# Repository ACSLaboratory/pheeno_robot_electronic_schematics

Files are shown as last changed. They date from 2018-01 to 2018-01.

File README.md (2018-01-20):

# pheeno_robot_electronic_schematics

## Pheeno Version 2.0

This is the ACSLab GitHub repository for the files relating to the electronic construction of the Pheeno robot platform. Pheeno is designed to be an inexpensive (cost of parts = $420), research-level platform for multi-robot experiments, robotics education, and outreach activities. This repository will be updated with additional modules, code, and improvements to existing modules as they are developed.

Thanks for checking out the robot!

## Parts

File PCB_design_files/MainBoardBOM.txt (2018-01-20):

"Id";"Designator";"Package";"Quantity";"Designation";"Supplier and ref";
1;"P9";"Pin_Header_Straight_1x04";1;"GPIO JUMPER";;;
2;"IRLF1,IRR1,IRB1,IRF1,IRL1,IRRF1";"GP2Y0A41SK0F";6;"GP2Y0A41SK0F";;;
3;"C17,C16,C15,C14,C13,C12,C11,C10,C9,C8,C7,C3";"C_Rect_L7_W2_P5";12;"0.1uF";;;
4;"C2,C1";"C_Rect_L7_W2_P5";2;"1uF";;;
5;"C4";"C_Radial_D10_L25_P5";1;"1000uF";;;
6;"P2";"Pin_Header_Straight_1x02";1;"Raspberry Pi Power";;;
7;"R1";"Resistor_Horizontal_RM7mm";1;"61.9k";;;
8;"R2,R3,R5";"Resistor_Horizontal_RM7mm";3;"49.9k";;;
9;"R4,R6";"Resistor_Horizontal_RM7mm";2;"1M";;;
10;"R8";"Resistor_Horizontal_RM7mm";1;"30k";;;
11;"R9,R14,R15,R16,R17,R18,R19";"Resistor_Horizontal_RM7mm";7;"10k";;;
12;"R10";"Resistor_Horizontal_RM7mm";1;"499";;;
13;"P1";"Molex_KK-6410-02_02x2.54mm_Straight";1;"12V Power";;;
14;"BT1";"Pin_Header_Straight_1x02";1;"11.1V";;;
15;"C5";"C_Radial_D10_L16_P5";1;"470uF";;;
16;"C6,C18,C19,C20,C21,C22,C23";"C_Radial_D4_P1.5";7;"10uF";;;
17;"D1";"Molex_KK-6410-02_02x2.54mm_Straight";1;"LED";;;
18;"IMU1";"Pololu_MiniIMU_v5";1;"Pololu_MinIMU_v5";;;
19;"MD1,MD2";"AdaFruit_TB6612";2;"AdaFruit_TB6612";;;
20;"OA1";"ICL7611";1;"ICL7611";;;
21;"P3";"Socket_MOLEX-KK-RM2-54mm_Lock_3pin_straight";1;"Color Control GPIO";;;
22;"P4";"Pin_Header_Straight_1x03";1;"Camera Servo Control";;;
23;"P5";"Molex_KK-6410-06_06x2.54mm_Straight";1;"RHBridge_Right Motor Connector";;;
24;"P6";"Molex_KK-6410-06_06x2.54mm_Straight";1;"RHBridge_Left Motor Connector";;;
25;"Q1";"IRF9530";1;"IRF9530";;;
26;"R7";"Resistor_Horizontal_RM7mm";1;"121";;;
27;"SW1";"Molex_KK-6410-02_02x2.54mm_Straight";1;"MainPowerSwitch";;;
28;"SW2";"Molex_KK-6410-02_02x2.54mm_Straight";1;"RPi_PowerSwitch";;;
29;"U1";"LP2950";1;"LP2950";;;
30;"U2,U3,U4,U5,U7";"OKI-78SR";5;"OKI-78SR";;;
31;"REF**,REF**,REF**,REF**";"MountingHole_3.2mm_M3";4;"MountingHole_3.2mm_M3";;;
32;"U6";"Teensy3.2";1;"Teensy3.2";;;
33;"P7";"Molex_KK-6410-06_06x2.54mm_Straight";1;"LHBridge_Right Motor Connector";;;
34;"P8";"Molex_KK-6410-06_06x2.54mm_Straight";1;"LHBridge_Left Motor Connector";;;

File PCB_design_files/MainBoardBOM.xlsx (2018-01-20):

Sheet: MainBoardBOM
Id | Designator | Package | Quantity | Designation | Supplier | Link | Cost | Total Cost | Note
1 | P9 | Pin_Header_Straight_1x04 | 4 | GPIO JUMPER | Digikey | https://www.digikey.com/product-detail/en/sullins-connector-solutions/PEC36SAAN/S1012E-36-ND/859153 | $1.57 | $0.17 | Strip of 36 unshrouded straight male breakaway headers.
2 | IRLF1,IRR1,IRB1,IRF1,IRL1,IRRF1 | GP2Y0A41SK0F | 6 | GP2Y0A41SK0F | Digikey | http://www.digikey.com/product-detail/en/sharp-microelectronics/GP2Y0A41SK0F/425-2819-ND/3884447 | $8.95 | $53.70 | 4-30 cm sensing model.
3 | C17,C16,C15,C14,C13,C12,C11,C10,C9,C8,C7,C3 | C_Rect_L7_W2_P5 | 12 | 0.1uF | Digikey | https://www.digikey.com/product-detail/en/tdk-corporation/FK28X7R1H104K/445-5258-ND/2256738 | $0.29 | $3.48
4 | C2,C1 | C_Rect_L7_W2_P5 | 2 | 1uF | Digikey | https://www.digikey.com/product-detail/en/nichicon/UMA1H010MCD2TP/493-10419-1-ND/4312678 | $0.26 | $0.52
5 | C4 | C_Radial_D10_L25_P5 | 1 | 1000uF | Digikey | https://www.digikey.com/product-detail/en/panasonic-electronic-components/ECA-1CHG102/P5533-ND/245132 | $0.69 | $0.69
6 | P2 | Pin_Header_Straight_1x02 | 1 | Raspberry Pi Power | N/A | N/A | $0.00 | $0.00 | This is a hole for the USB power cord.
7 | R1 | Resistor_Horizontal_RM7mm | 1 | 61.9k | Digikey | https://www.digikey.com/product-detail/en/yageo/MFR-25FBF52-61K9/61.9KXBK-ND/13432 | $0.10 | $0.10
8 | R2,R3,R5 | Resistor_Horizontal_RM7mm | 3 | 49.9k | Digikey | https://www.digikey.com/product-detail/en/yageo/MFR-25FBF52-49K9/49.9KXBK-ND/13414 | $0.10 | $0.30
9 | R4,R6 | Resistor_Horizontal_RM7mm | 2 | 1M | Digikey | https://www.digikey.com/product-detail/en/yageo/MFR-25FBF52-1M/1.00MXBK-ND/13714 | $0.10 | $0.20
10 | R8 | Resistor_Horizontal_RM7mm | 1 | 30k | Digikey | https://www.digikey.com/product-detail/en/yageo/MFR-25FBF52-29R4/29.4XBK-ND/12693 | $0.10 | $0.10
11 | R9,R14,R15,R16,R17,R18,R19 | Resistor_Horizontal_RM7mm | 7 | 10k | Digikey | https://www.digikey.com/product-detail/en/yageo/MFR-25FBF52-10K/10.0KXBK-ND/13219 | $0.10 | $0.70
12 | R10 | Resistor_Horizontal_RM7mm | 1 | 499 | Digikey | https://www.digikey.com/product-detail/en/yageo/MFR-25FBF52-499R/499XBK-ND/12939 | $0.10 | $0.10
13 | P1 | Molex_KK-6410-02_02x2.54mm_Straight | 1 | 12V Power | Digikey | https://www.digikey.com/product-detail/en/molex-llc/0022232021/WM4200-ND/26667 | $0.16 | $0.16
14 | BT1 | Pin_Header_Straight_1x02 | 1 | 11.1V | Digikey | https://www.digikey.com/product-detail/en/molex-llc/0022232021/WM4200-ND/26667 | $0.16 | $0.16
15 | C5 | C_Radial_D10_L16_P5 | 1 | 470uF | Digikey | https://www.digikey.com/product-detail/en/panasonic-electronic-components/EEU-FR1E471B/P15361CT-ND/3072241 | $0.84 | $0.84
16 | C6,C18,C19,C20,C21,C22,C23 | C_Radial_D4_P1.5 | 7 | 10uF | Digikey | https://www.digikey.com/product-detail/en/panasonic-electronic-components/EEA-GA1E100H/P15799CT-ND/3831166 | $0.24 | $1.68
17 | D1 | Molex_KK-6410-02_02x2.54mm_Straight | 1 | LED | Digikey | https://www.digikey.com/product-detail/en/cree-inc/C503B-GAN-CB0F0791/C503B-GAN-CB0F0791-ND/1922938 | $0.24 | $0.24
18 | IMU1 | Pololu_MiniIMU_v5 | 1 | Pololu_MinIMU_v5 | Pololu | https://www.pololu.com/product/2738 | $15.95 | $15.95
19 | MD1,MD2 | AdaFruit_TB6612 | 2 | AdaFruit_TB6612 | Ada Fruit | https://www.adafruit.com/products/2448 | $4.95 | $9.90
20 | OA1 | ICL7611 | 1 | ICL7611 | Digikey | https://www.digikey.com/product-detail/en/intersil/ICL7611DCPAZ/ICL7611DCPAZ-ND/821481 | $1.77 | $1.77 | Comparator (Op Amp)
21 | P3 | Socket_MOLEX-KK-RM2-54mm_Lock_3pin_straight | 1 | Color Control GPIO | Digikey | https://www.digikey.com/product-detail/en/molex-llc/0022232031/WM4201-ND/26669 | $0.23 | $0.23
22 | P4 | Pin_Header_Straight_1x03 | 3 | Camera Servo Control | Digikey | https://www.digikey.com/product-detail/en/sullins-connector-solutions/PEC36SAAN/S1012E-36-ND/859153 | $1.57 | $0.13 | Strip of 36 unshrouded straight male breakaway headers.
23 | P5 | Molex_KK-6410-06_06x2.54mm_Straight | 1 | RHBridge_Right Motor Connector | Digikey | https://www.digikey.com/product-detail/en/molex-llc/0022232061/WM4204-ND/26675 | $0.41 | $0.41
24 | P6 | Molex_KK-6410-06_06x2.54mm_Straight | 1 | RHBridge_Left Motor Connector | Digikey | https://www.digikey.com/product-detail/en/molex-llc/0022232061/WM4204-ND/26675 | $0.41 | $0.41
25 | Q1 | IRF9530 | 1 | IRF9530 | Digikey | https://www.digikey.com/product-detail/en/vishay-siliconix/IRF9530PBF/IRF9530PBF-ND/811815 | $1.38 | $1.38
26 | R7 | Resistor_Horizontal_RM7mm | 1 | 121 | Digikey | https://www.digikey.com/product-detail/en/yageo/MFR-25FBF52-121R/121XBK-ND/12812 | $0.10 | $0.10
27 | SW1 | Molex_KK-6410-02_02x2.54mm_Straight | 1 | MainPowerSwitch | Digikey | https://www.digikey.com/product-detail/en/molex-llc/0022232021/WM4200-ND/26667 | $0.16 | $0.16
28 | SW2 | Molex_KK-6410-02_02x2.54mm_Straight | 1 | RPi_PowerSwitch | Digikey | https://www.digikey.com/product-detail/en/molex-llc/0022232021/WM4200-ND/26667 | $0.16 | $0.16
29 | U1 | LP2950 | 1 | LP2950 | Digikey | https://www.digikey.com/product-detail/en/texas-instruments/LP2950ACZ-5.0-NOPB/LP2950ACZ-5.0NS-NOPB-ND/148221 | $0.83 | $0.83
30 | U2,U3,U4,U5,U7 | OKI-78SR | 5 | OKI-78SR | Digikey | https://www.digikey.com/product-detail/en/murata-power-solutions-inc/OKI-78SR-5-1.5-W36-C/811-2196-5-ND/2259781 | $4.31 | $21.55 | Switching Regulator for power.
31 | REF**,REF**,REF**,REF** | MountingHole_3.2mm_M3 | 4 | MountingHole_3.2mm_M3 | N/A | N/A | $0.00 | $0.00 | Hole for mounting screws.
32 | U6 | Teensy3.2 | 1 | Teensy3.2 | PJRC | https://www.pjrc.com/store/teensy32.html | $19.80 | $19.80
33 | P7 | Molex_KK-6410-06_06x2.54mm_Straight | 1 | LHBridge_Right Motor Connector | Digikey | https://www.digikey.com/product-detail/en/molex-llc/0022232061/WM4204-ND/26675 | $0.41 | $0.41
34 | P8 | Molex_KK-6410-06_06x2.54mm_Straight | 1 | LHBridge_Left Motor Connector | Digikey | https://www.digikey.com/product-detail/en/molex-llc/0022232061/WM4204-ND/26675 | $0.41 | $0.41
 | Main Board Total Cost! | $136.75

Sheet: Additional Components
Designation | Quantity | Supplier | Link | Cost | Total Cost | Note
IR Mount Housing | 6 | Digikey | http://www.digikey.com/product-detail/en/jst-sales-america-inc/PHR-3/455-1126-ND/527357 | $0.10 | $0.60 | For attaching the IR to the PCB in a solid way.
IR Mounting Pins | 6 | Digikey | https://www.digikey.com/product-detail/en/harwin-inc/M22-2010305/952-2274-ND/3728238 | $0.15 | $0.90 | For attaching the IR to the PCB in a solid way.
IR Connection Terminals (24-30) | 18 | Digikey | http://www.digikey.com/product-detail/en/jst-sales-america-inc/SPH-002T-P0.5S/455-1127-1-ND/527358 | $0.10 | $1.80 | For attaching the IR to the PCB in a solid way.
Molex Connector Housing (6 pins) | 2 | Digikey | http://www.digikey.com/product-detail/en/molex-llc/0022013067/WM2004-ND/26439 | $0.31 | $0.62 | For attaching motors to the PCB.
Molex Connector Housing (3 pins) | 1 | Digikey | http://www.digikey.com/product-detail/en/molex-llc/0022013037/WM2001-ND/26433 | $0.19 | $0.19 | For attaching NeoPixels to the PCB.
Molex Connector Housing (2 pins) | 2 | Digikey | http://www.digikey.com/product-detail/en/molex-llc/0022013027/WM2000-ND/26431 | $0.13 | $0.26 | For attaching switches to the PCB.
Molex Connection Terminals (22-30) | 20 | Digikey | https://www.digikey.com/product-detail/en/molex-llc/0008550102/WM2312-ND/172056 | $0.27 | $5.40 | For attaching switches and motors to the PCB.
Rocker Switch | 2 | Digikey | https://www.digikey.com/product-detail/en/te-connectivity-alcoswitch-switches/PRASA1-16F-BB0BW/450-1810-ND/529580 | $1.06 | $2.12 | Turning on and off the robot/pi.
SMC Header Pins for Teensy | 1 | Digikey | https://www.digikey.com/product-detail/en/molex-llc/0015912140/WM17453-ND/614769 | $1.04 | $1.04 | Allows access to SMC pins on Teensy.
Male Header Pins for Teensy | 32 | Digikey | https://www.digikey.com/product-detail/en/sullins-connector-solutions/PEC36SAAN/S1012E-36-ND/859153 | $1.57 | $1.40 | Strip of 36 unshrouded straight male breakaway headers.
Female Header Pins to Remove Teensy (14 Pins) | 2 | Digikey | https://www.digikey.com/product-detail/en/sullins-connector-solutions/PPTC141LFBN-RC/S7012-ND/810152 | $1.14 | $2.28
Female Header Pins to Remove Teensy (5 Pins) | 1 | Digikey | https://www.digikey.com/product-detail/en/sullins-connector-solutions/PPTC051LFBN-RC/S6103-ND/807239 | $0.62 | $0.62
USB Cord for Teensy to Raspberry Pi | 1 | OKRAY | https://www.amazon.com/gp/product/B00R5GZJR6/ref=s9_dcacsd_dcoop_bw_c_x_5_w | $8.39 | $0.84 | Pack of 10
USB Cord to Power Raspberry Pi | 1 | Ada Fruit | https://www.adafruit.com/products/3030 | $2.95 | $1.48 | USB Y split, should be able to get two power cords from it!
Header Pins for Motor Boards | 32 | Digikey | https://www.digikey.com/product-detail/en/sullins-connector-solutions/PEC36SAAN/S1012E-36-ND/859153 | $1.57 | $1.40 | Strip of 36 unshrouded straight male breakaway headers.
Jumper Wire for Extra Teensy GPIO | 1 | Sparkfun | https://www.sparkfun.com/products/10364 | $0.95 | $0.95 | 4 inch 4 pin female to female jumper
Header Pins for Extra Teensy GPIO | 4 | Digikey | https://www.digikey.com/product-detail/en/sullins-connector-solutions/PEC36SAAN/S1012E-36-ND/859153 | $1.57 | $0.17
Misc Cost |  |  |  |  | 20 | Wires, solder, screws, 3d printing material.
Additional Component Cost | $42.06

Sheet: Extras
Designation | Quantity | Supplier | Link | Cost | Total Cost | Note
Raspberry Pi 3.0 | 1 | Ada Fruit | https://www.adafruit.com/products/3055 | 39.9 | 39.9 | Can be exchanged for any previous model.
Raspberry Pi Camera | 1 | Ada Fruit | https://www.adafruit.com/products/3099 | 29.95 | 29.95
Micro Metal Gear Motors | 2 | Pololu | https://www.pololu.com/product/2203 | 16.95 | 33.9 | Currently using the 50:1 gear ratio low power, any other low power can be used
Encoders | 1 | Pololu | https://www.pololu.com/product/3081 | 8.95 | 8.95
Wheels | 1 | Pololu | https://www.pololu.com/product/1087 | 4.98 | 4.98
Additional Component Cost | $117.68

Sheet: Grand Total
GRAND TOTAL | $296.48
DISCLAIMER: THIS DOES NOT INCLUDE PCB FABRICATION COST!

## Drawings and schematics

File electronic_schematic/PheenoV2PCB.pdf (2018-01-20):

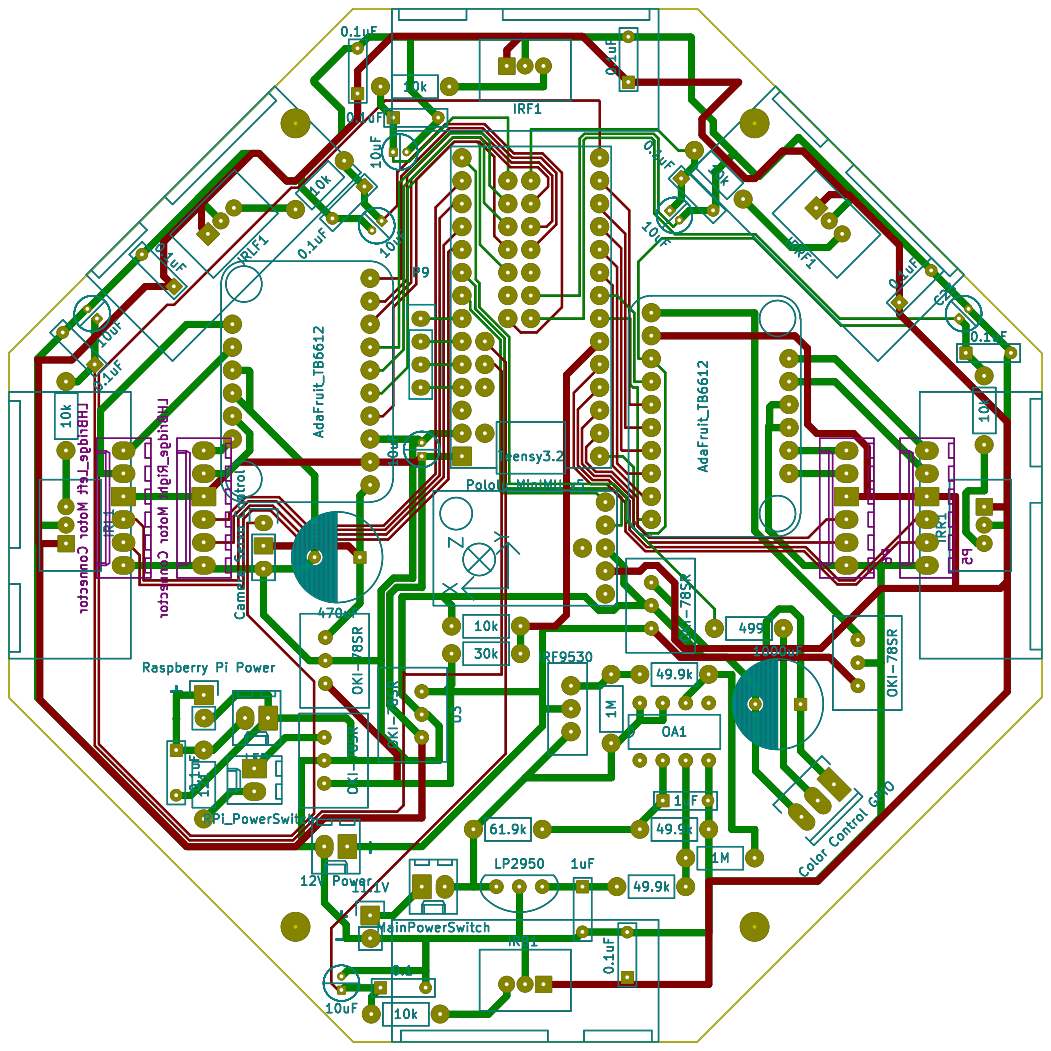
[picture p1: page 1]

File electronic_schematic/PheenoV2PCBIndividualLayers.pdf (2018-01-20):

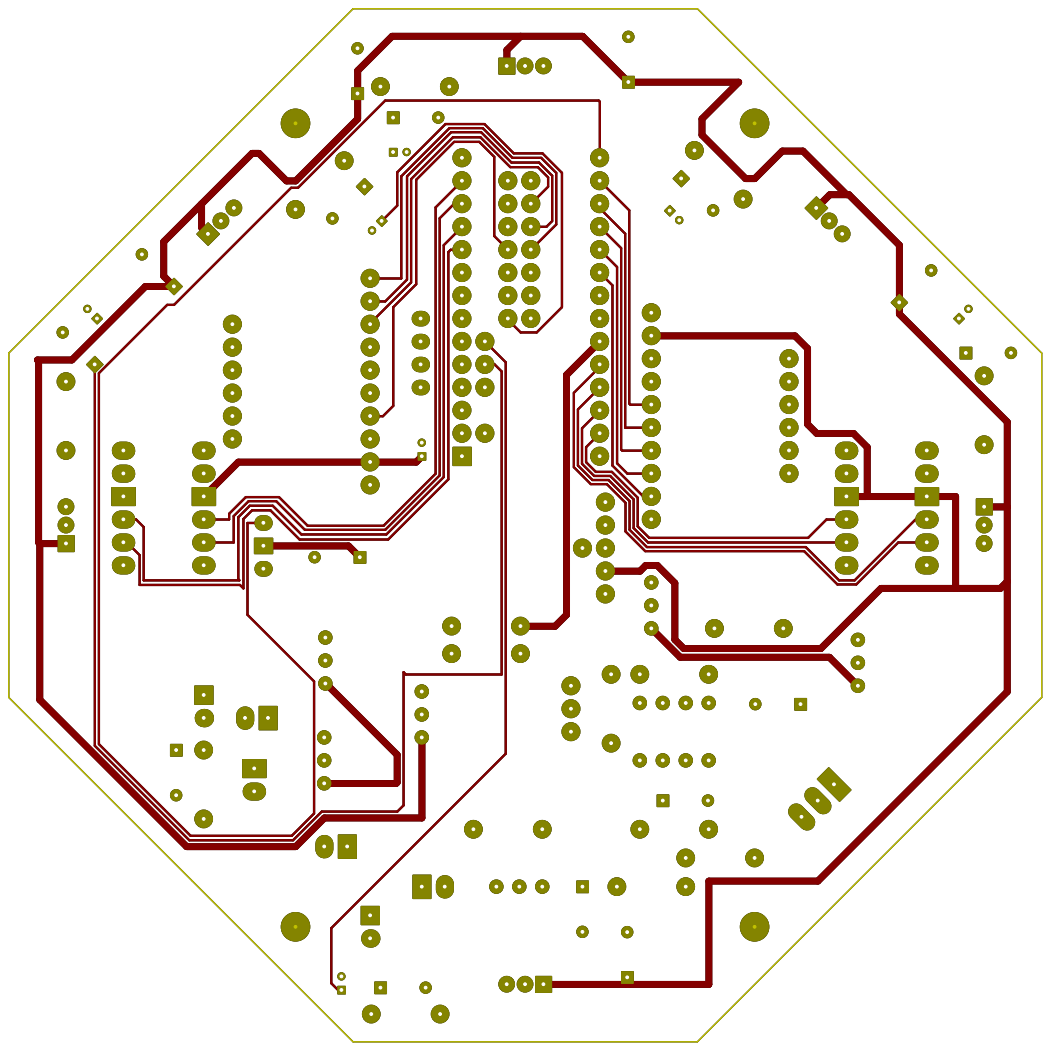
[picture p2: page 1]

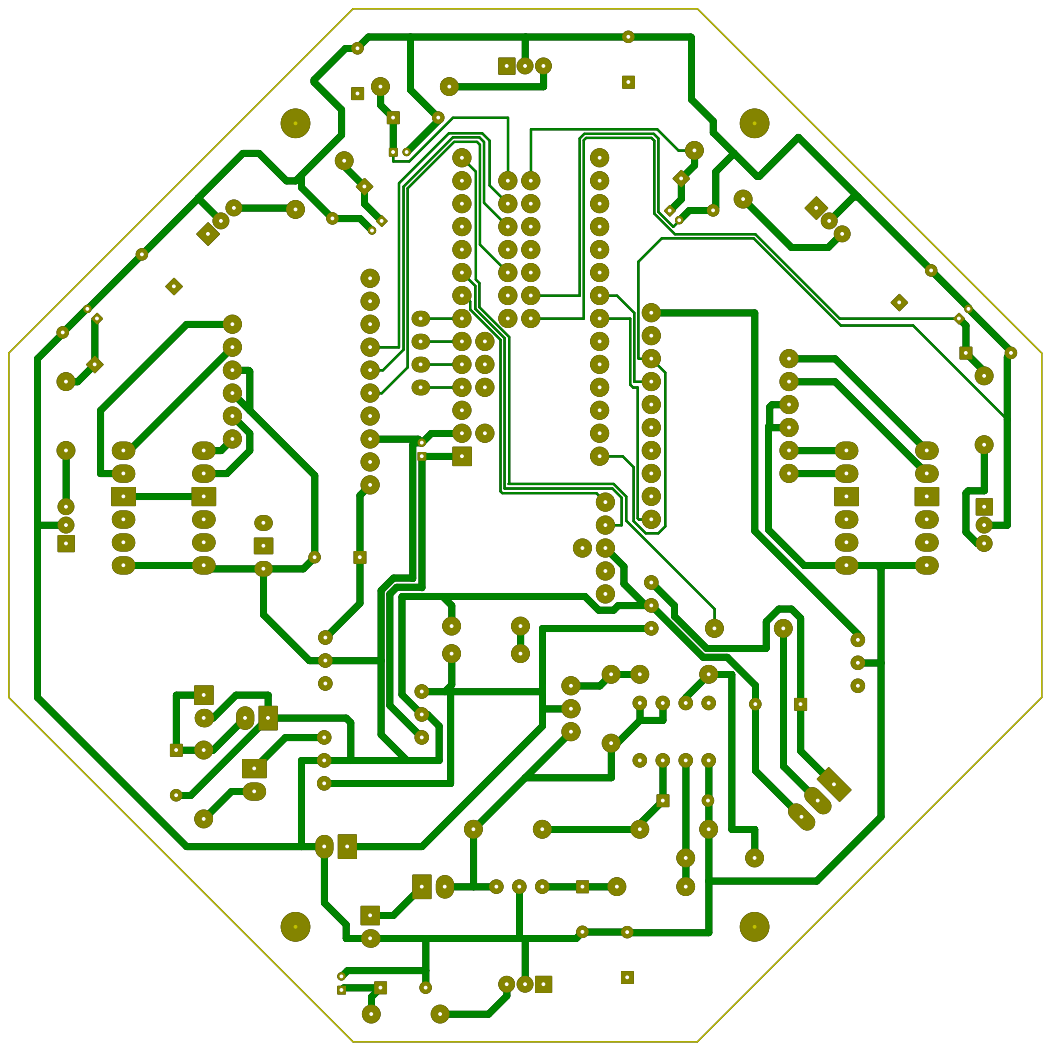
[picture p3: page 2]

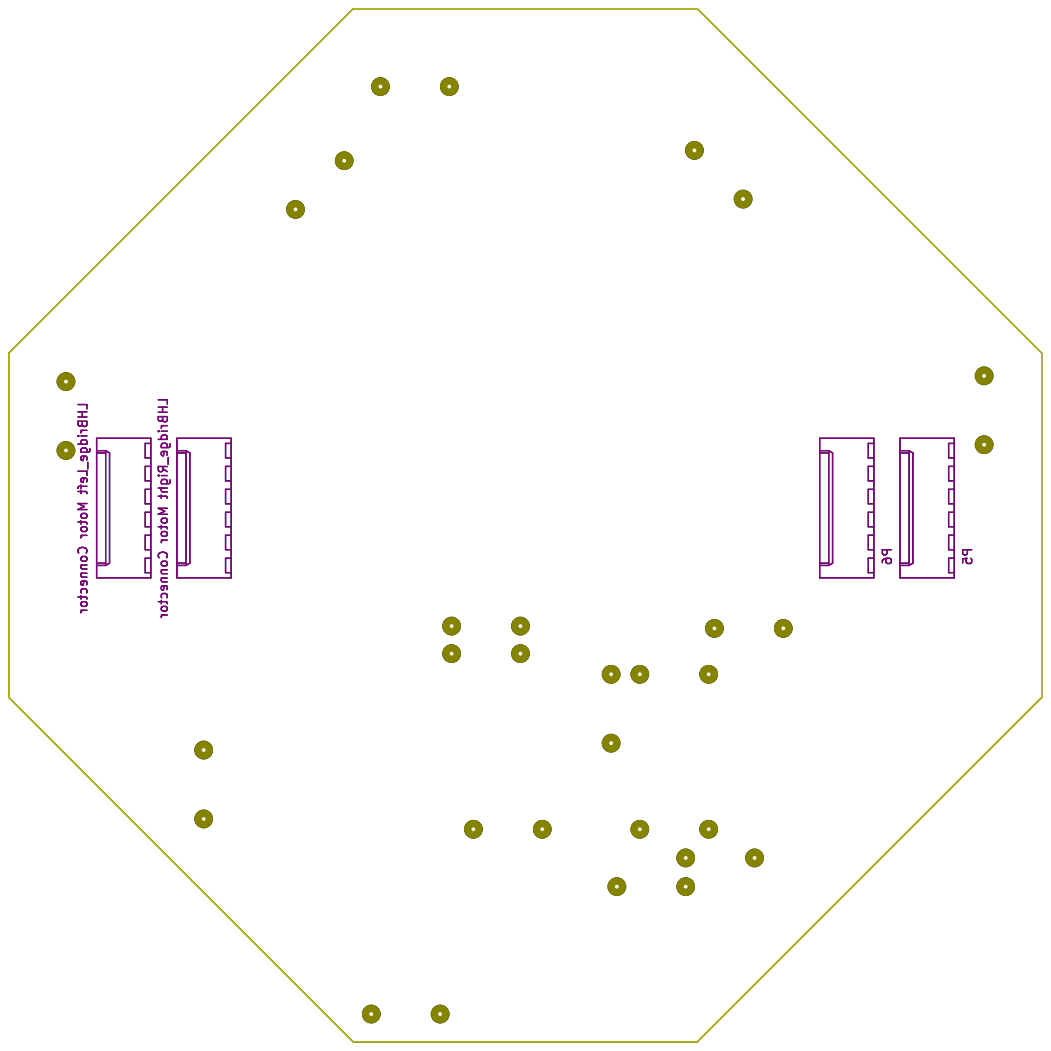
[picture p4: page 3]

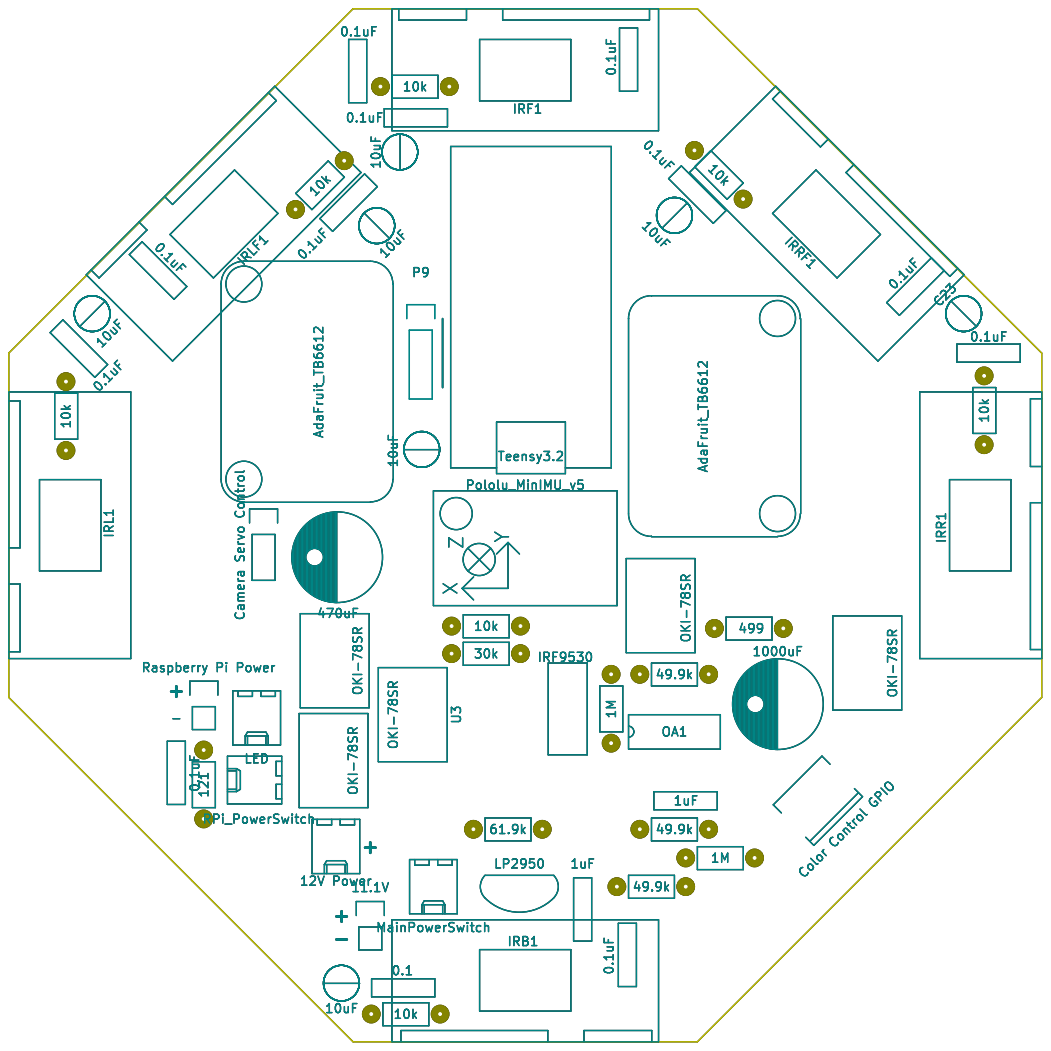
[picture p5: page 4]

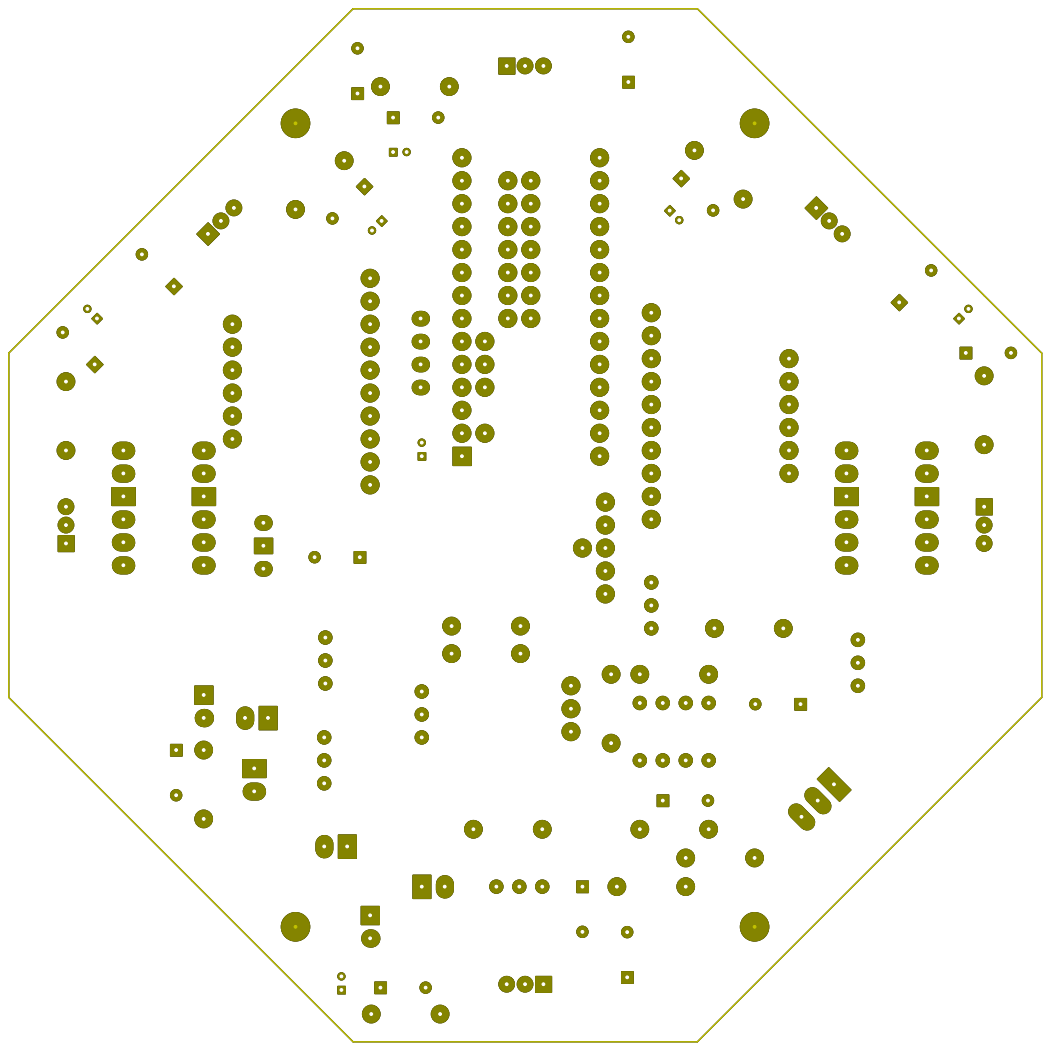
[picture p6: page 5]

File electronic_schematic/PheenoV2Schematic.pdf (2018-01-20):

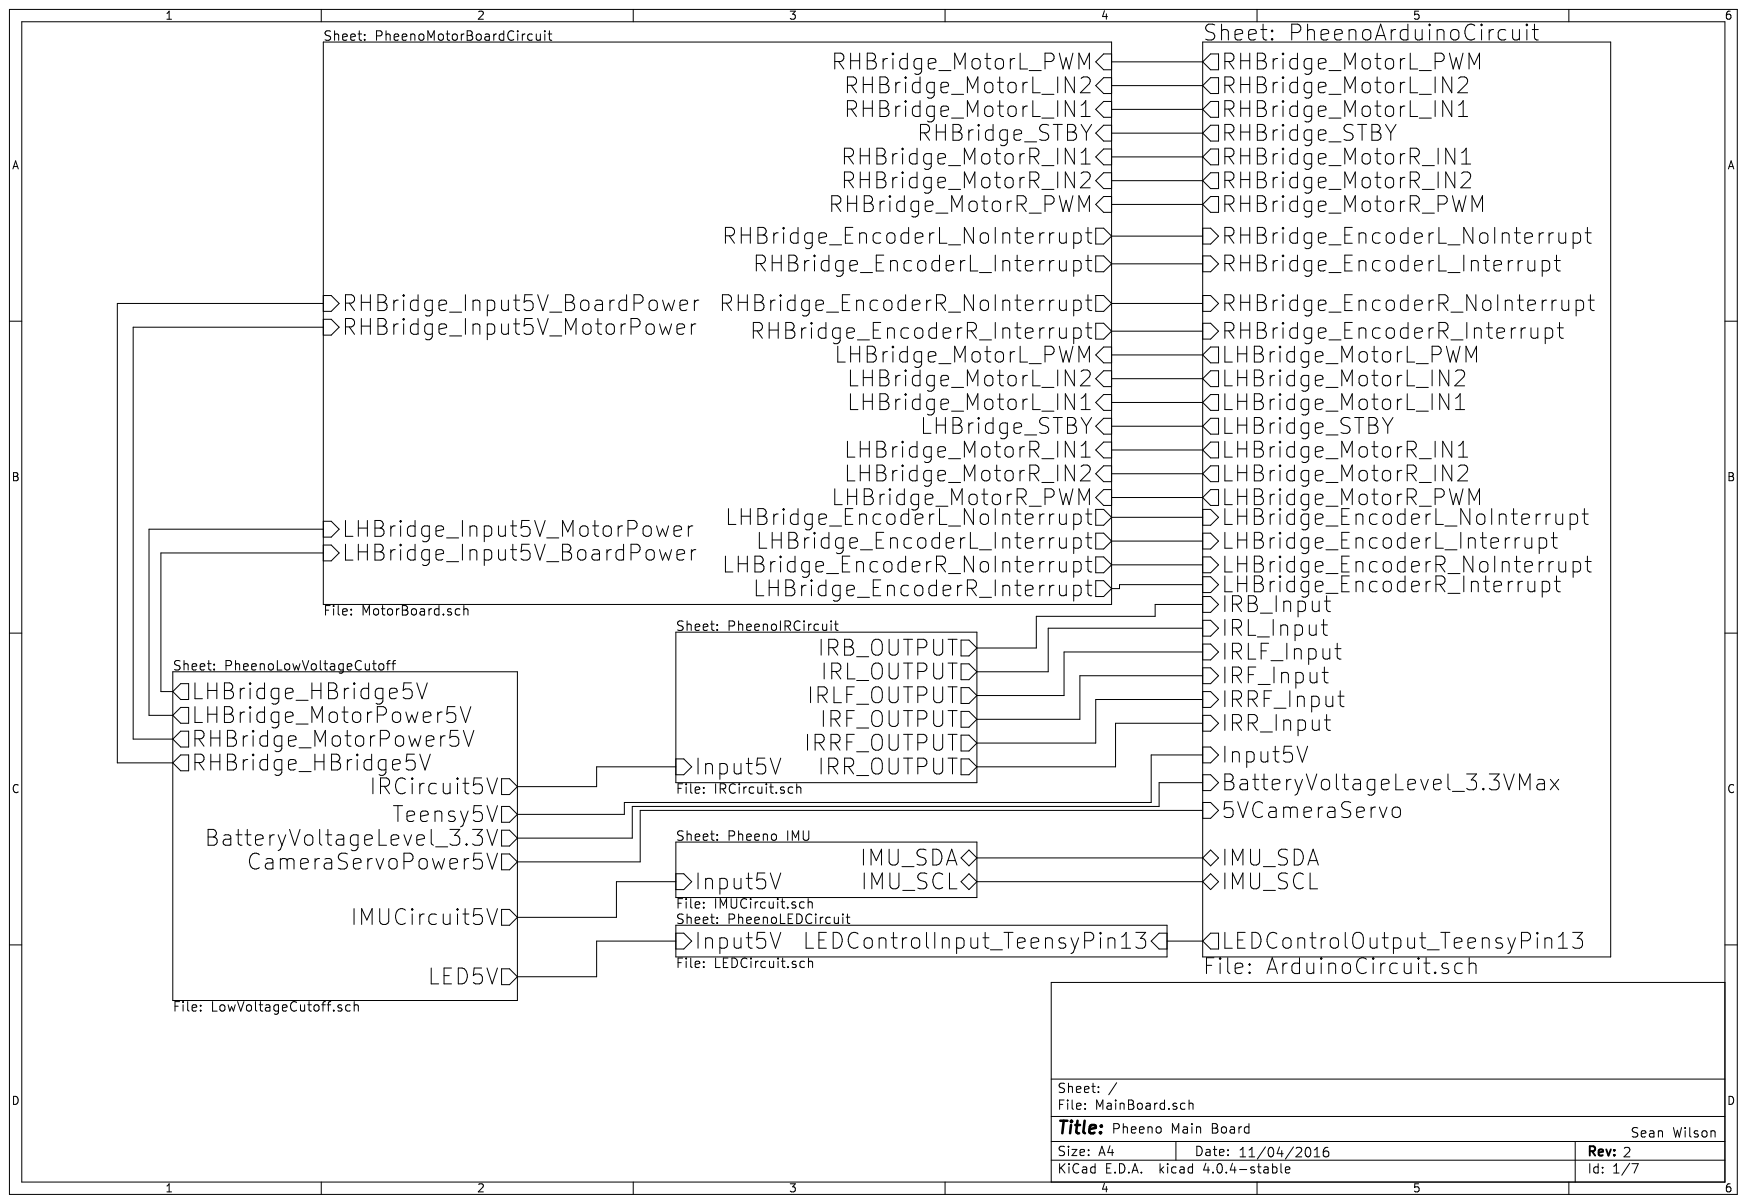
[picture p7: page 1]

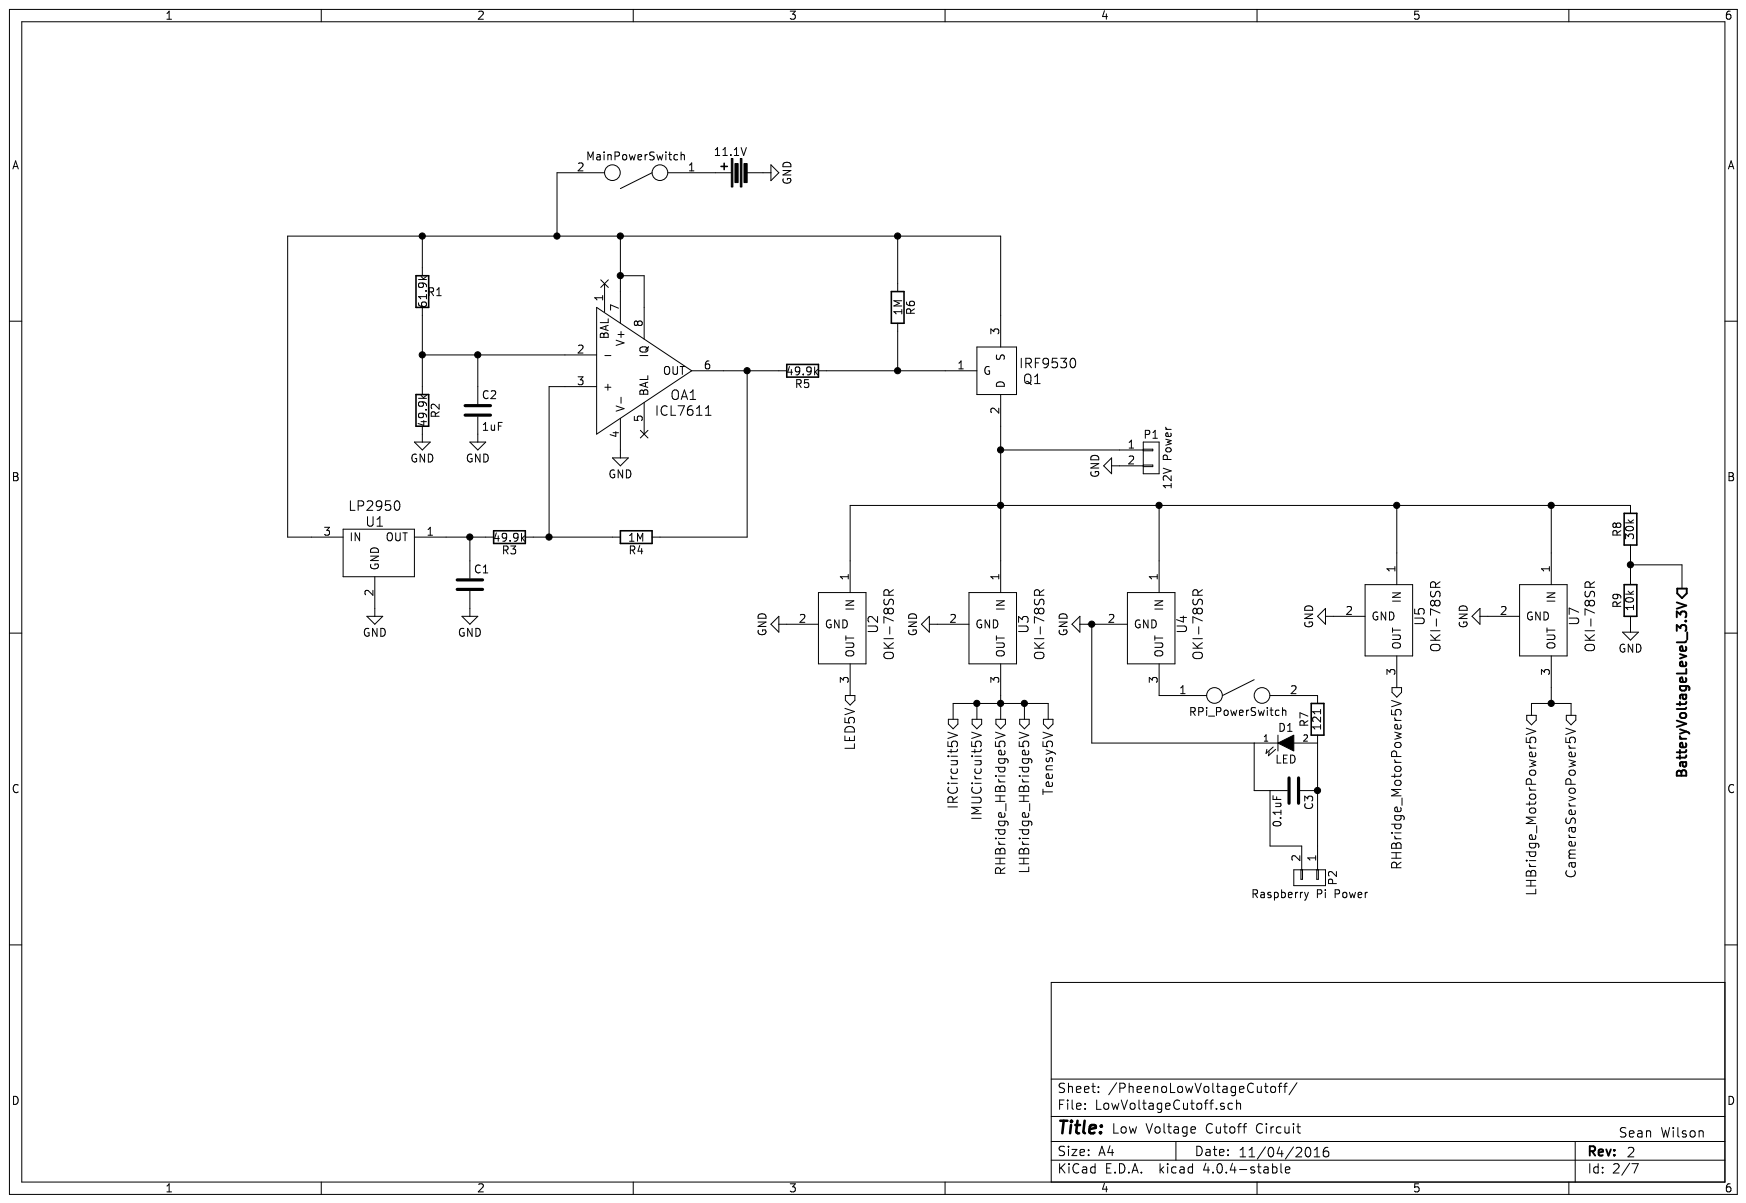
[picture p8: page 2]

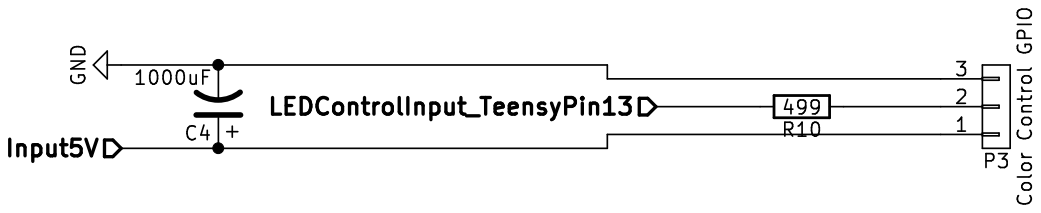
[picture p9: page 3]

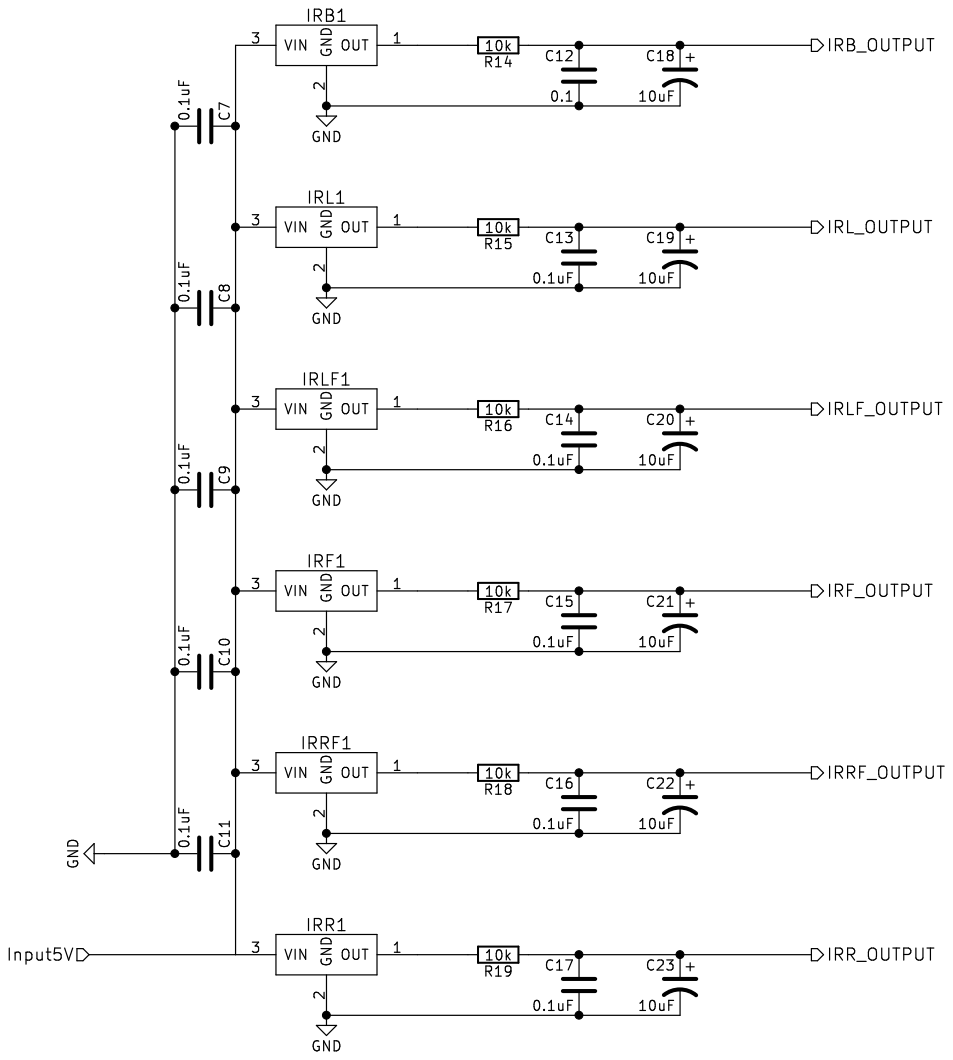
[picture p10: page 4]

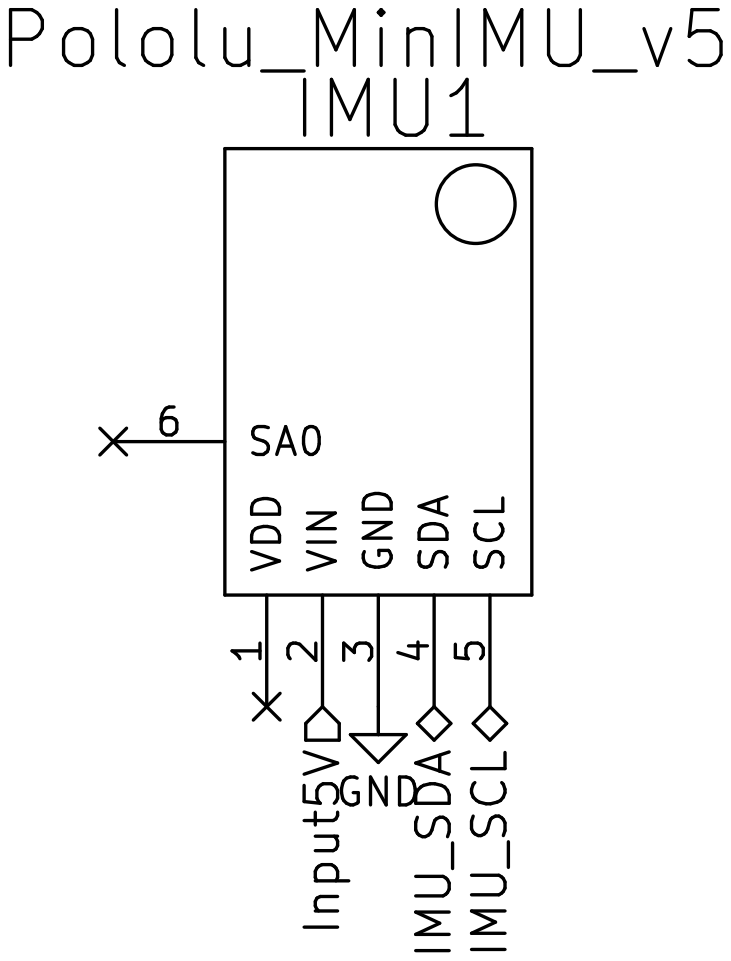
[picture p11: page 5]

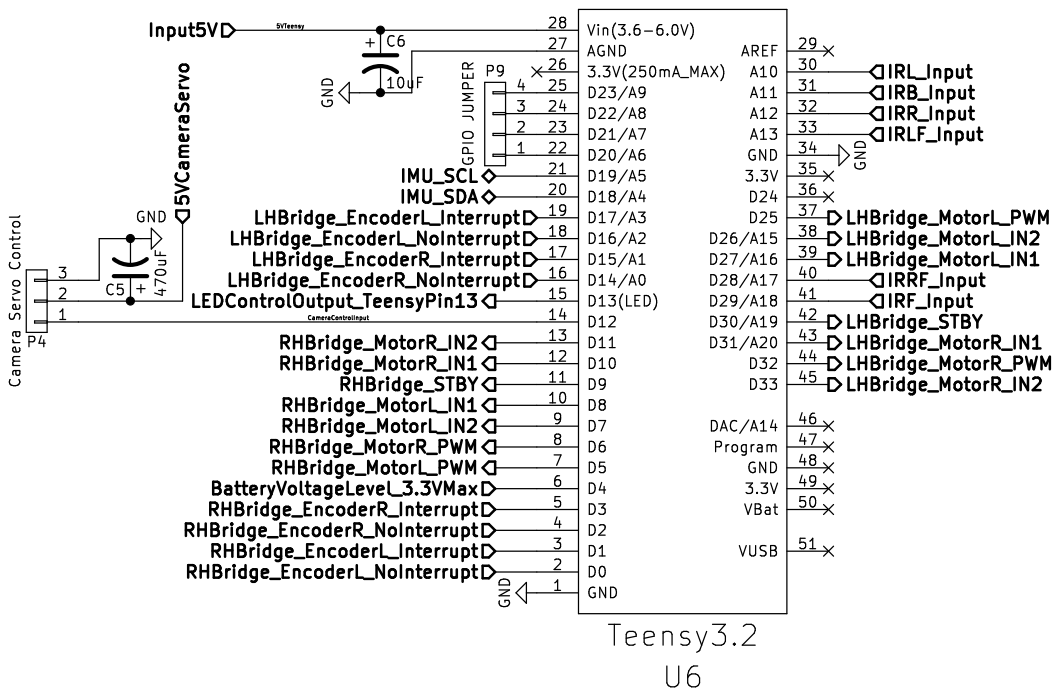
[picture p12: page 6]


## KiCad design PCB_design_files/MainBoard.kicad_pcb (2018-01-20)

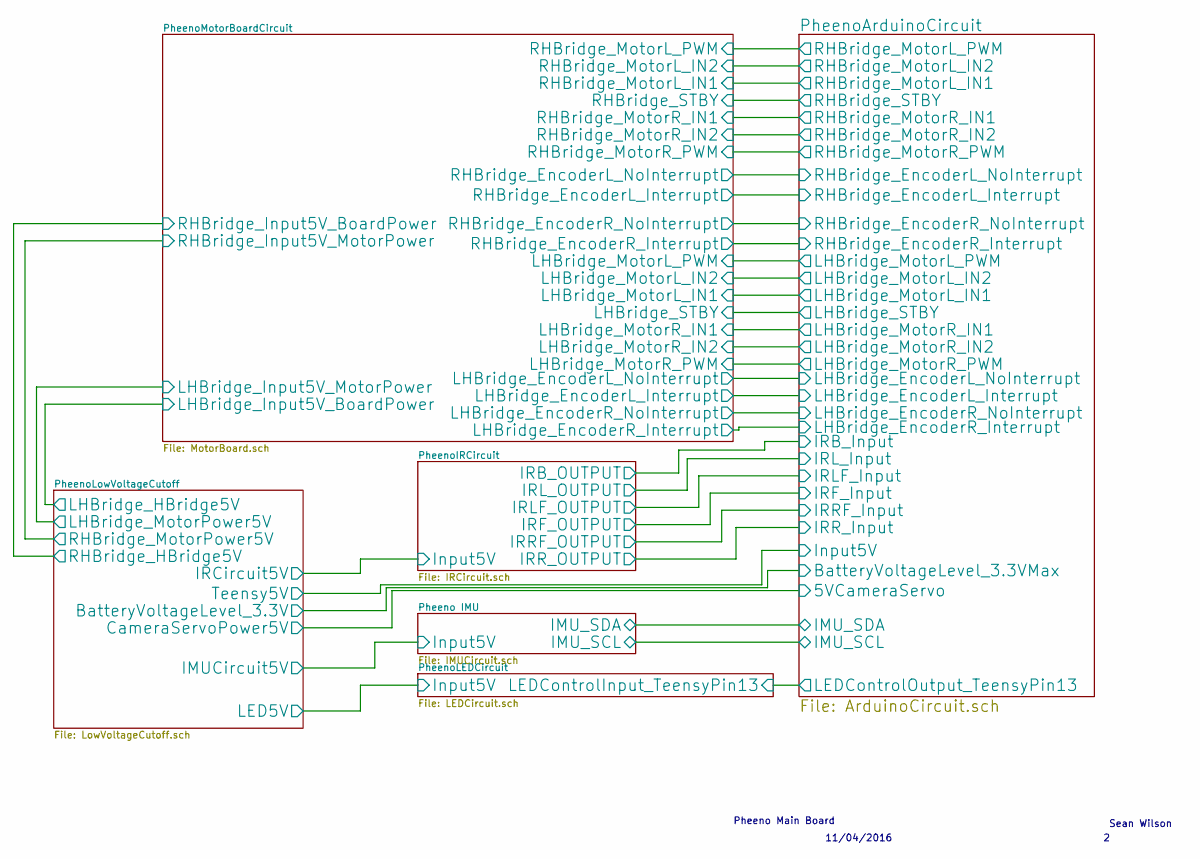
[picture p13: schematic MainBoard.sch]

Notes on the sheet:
Pheeno Main Board
11/04/2016
Sean Wilson

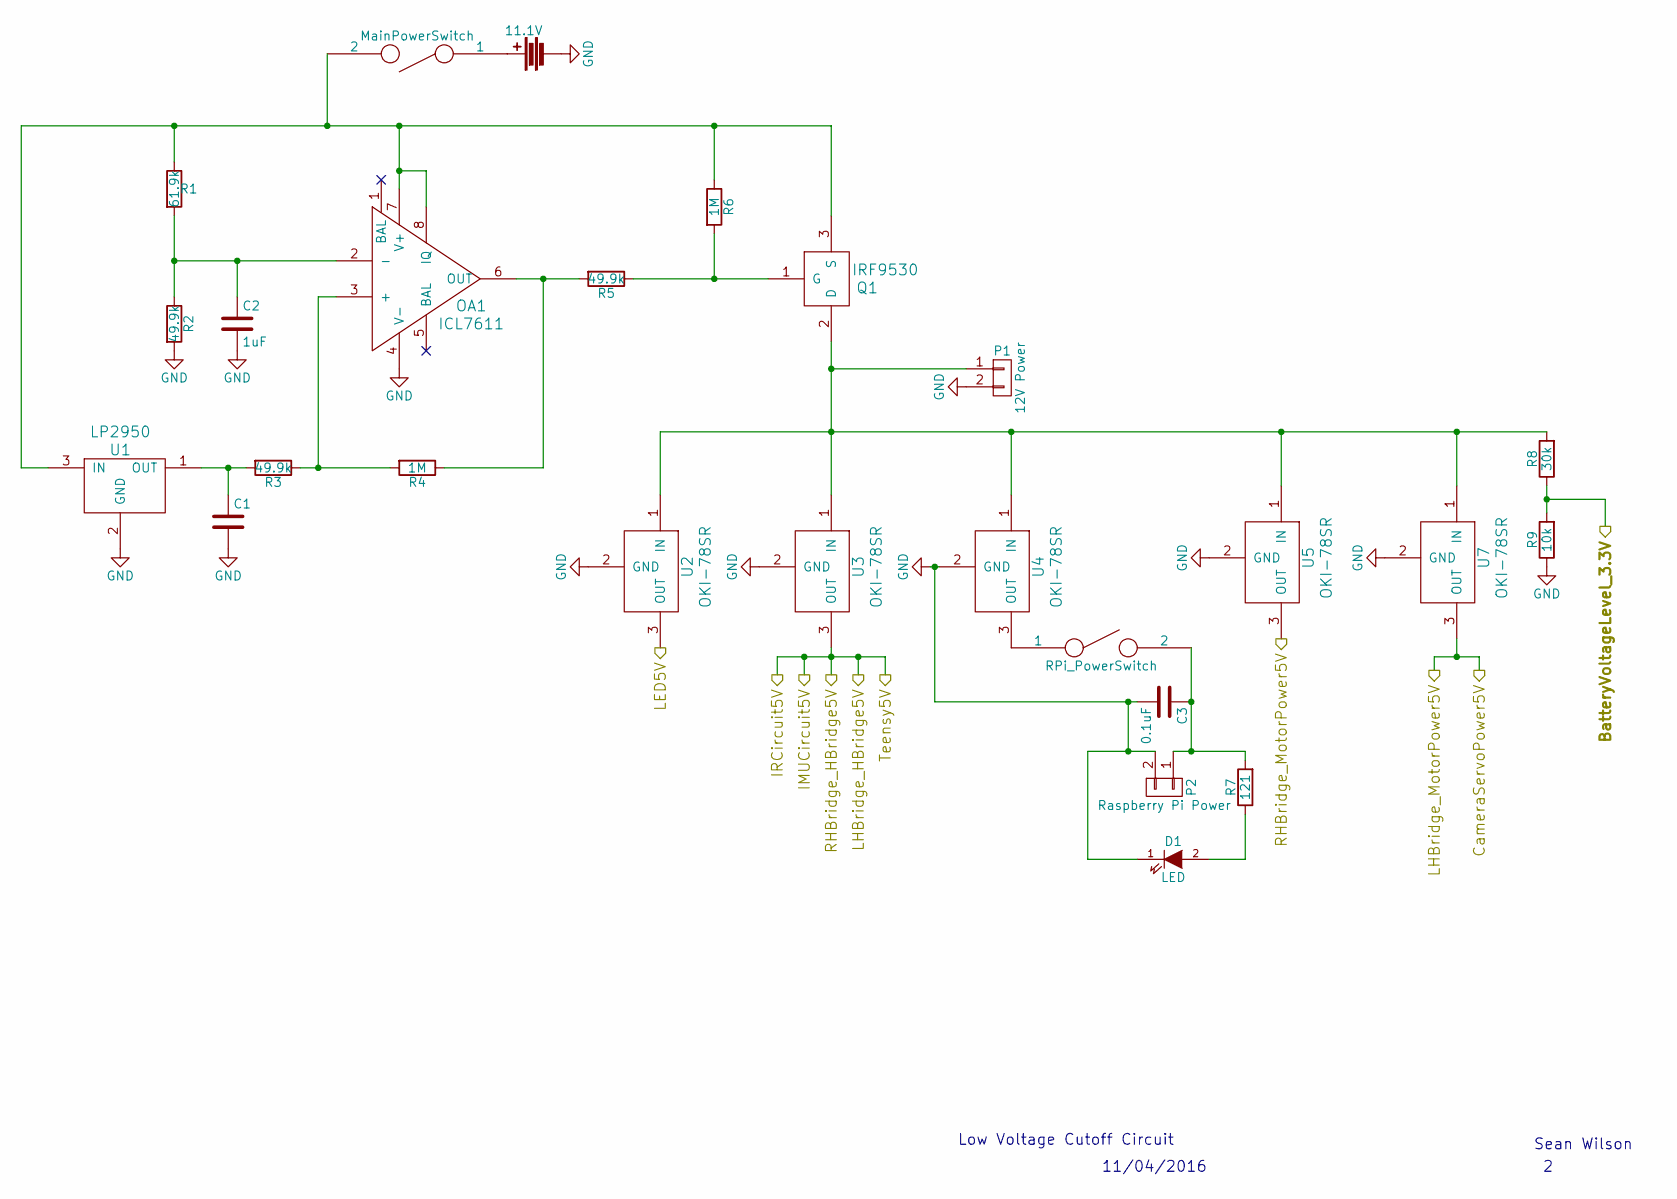
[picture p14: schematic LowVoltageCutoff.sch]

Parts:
BT1: 11.1V; Pin_Header_Straight_1x02
C1, C2: 1uF; C_Rect_L7_W2_P5
C3: 0.1uF; C_Rect_L7_W2_P5
D1: LED; Molex_KK-6410-02_02x2.54mm_Straight
OA1: ICL7611
P1: 12V Power; Molex_KK-6410-02_02x2.54mm_Straight
P2: Raspberry Pi Power; Pin_Header_Straight_1x02
Q1: IRF9530
R1: 61.9k; Resistor_Horizontal_RM7mm
R2, R3, R5: 49.9k; Resistor_Horizontal_RM7mm
R4, R6: 1M; Resistor_Horizontal_RM7mm
R7: 121; Resistor_Horizontal_RM7mm
R8: 30k; Resistor_Horizontal_RM7mm
R9: 10k; Resistor_Horizontal_RM7mm
SW1: MainPowerSwitch; Molex_KK-6410-02_02x2.54mm_Straight
SW2: RPi_PowerSwitch; Molex_KK-6410-02_02x2.54mm_Straight
U1: LP2950
U2, U3, U4, U5, U7: OKI-78SR

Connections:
/PheenoArduinoCircuit/5VCameraServo: U7.3 (OUT); also elsewhere on the board
/PheenoLEDCircuit/Input5V: U2.3 (OUT); also elsewhere on the board
/PheenoLowVoltageCutoff/BatteryVoltageLevel_3.3V: R8.1, R9.2; also elsewhere on the board
/PheenoLowVoltageCutoff/IMUCircuit5V: U3.3 (OUT); also elsewhere on the board
/PheenoMotorBoardCircuit/RHBridge_Input5V_MotorPower: U5.3 (OUT); also elsewhere on the board
GND: BT1.2, C1.2, C2.2, C3.2, D1.1 (K), OA1.4 (V-), P1.2, P2.2, R2.2, R9.1, U1.2 (GND), U2.2 (GND), U3.2 (GND), U4.2 (GND), U5.2 (GND), U7.2 (GND); also elsewhere on the board
unnamed: BT1.1, SW1.1
unnamed: C1.1, R3.2, U1.1 (OUT)
unnamed: C2.1, OA1.2 (-), R1.2, R2.1
unnamed: C3.1, P2.1, R7.2, SW2.2
unnamed: D1.2 (A), R7.1
unnamed: OA1.3 (+), R3.1, R4.2
unnamed: OA1.6 (OUT), R4.1, R5.2
unnamed: OA1.7 (V+), OA1.8 (IQ), Q1.3 (S), R1.1, R6.1, SW1.2, U1.3 (IN)
unnamed: P1.1, Q1.2 (D), R8.2, U2.1 (IN), U3.1 (IN), U4.1 (IN), U5.1 (IN), U7.1 (IN)
unnamed: Q1.1 (G), R5.1, R6.2
unnamed: SW2.1, U4.3 (OUT)

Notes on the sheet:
Low Voltage Cutoff Circuit
11/04/2016
Sean Wilson

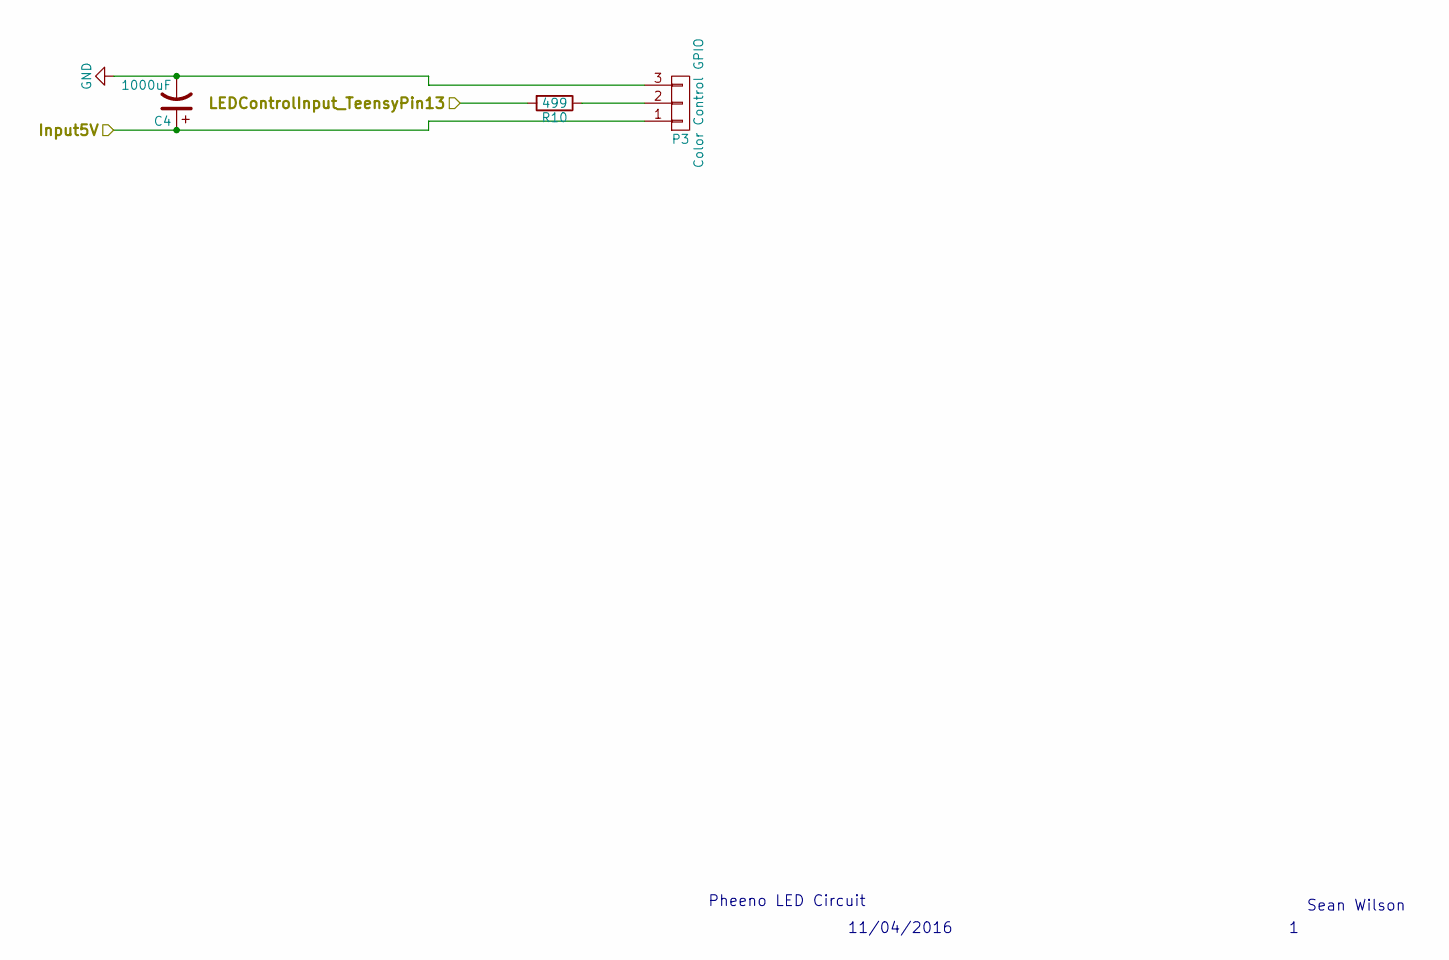
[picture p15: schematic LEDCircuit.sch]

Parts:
C4: 1000uF; C_Radial_D10_L25_P5
P3: Color Control GPIO; Socket_MOLEX-KK-RM2-54mm_Lock_3pin_straight
R10: 499; Resistor_Horizontal_RM7mm

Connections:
/PheenoLEDCircuit/Input5V: C4.1, P3.1; also elsewhere on the board
/PheenoLEDCircuit/LEDControlInput_TeensyPin13: R10.2; also elsewhere on the board
GND: C4.2, P3.3; also elsewhere on the board
unnamed: P3.2, R10.1

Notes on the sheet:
Pheeno LED Circuit
11/04/2016
Sean Wilson

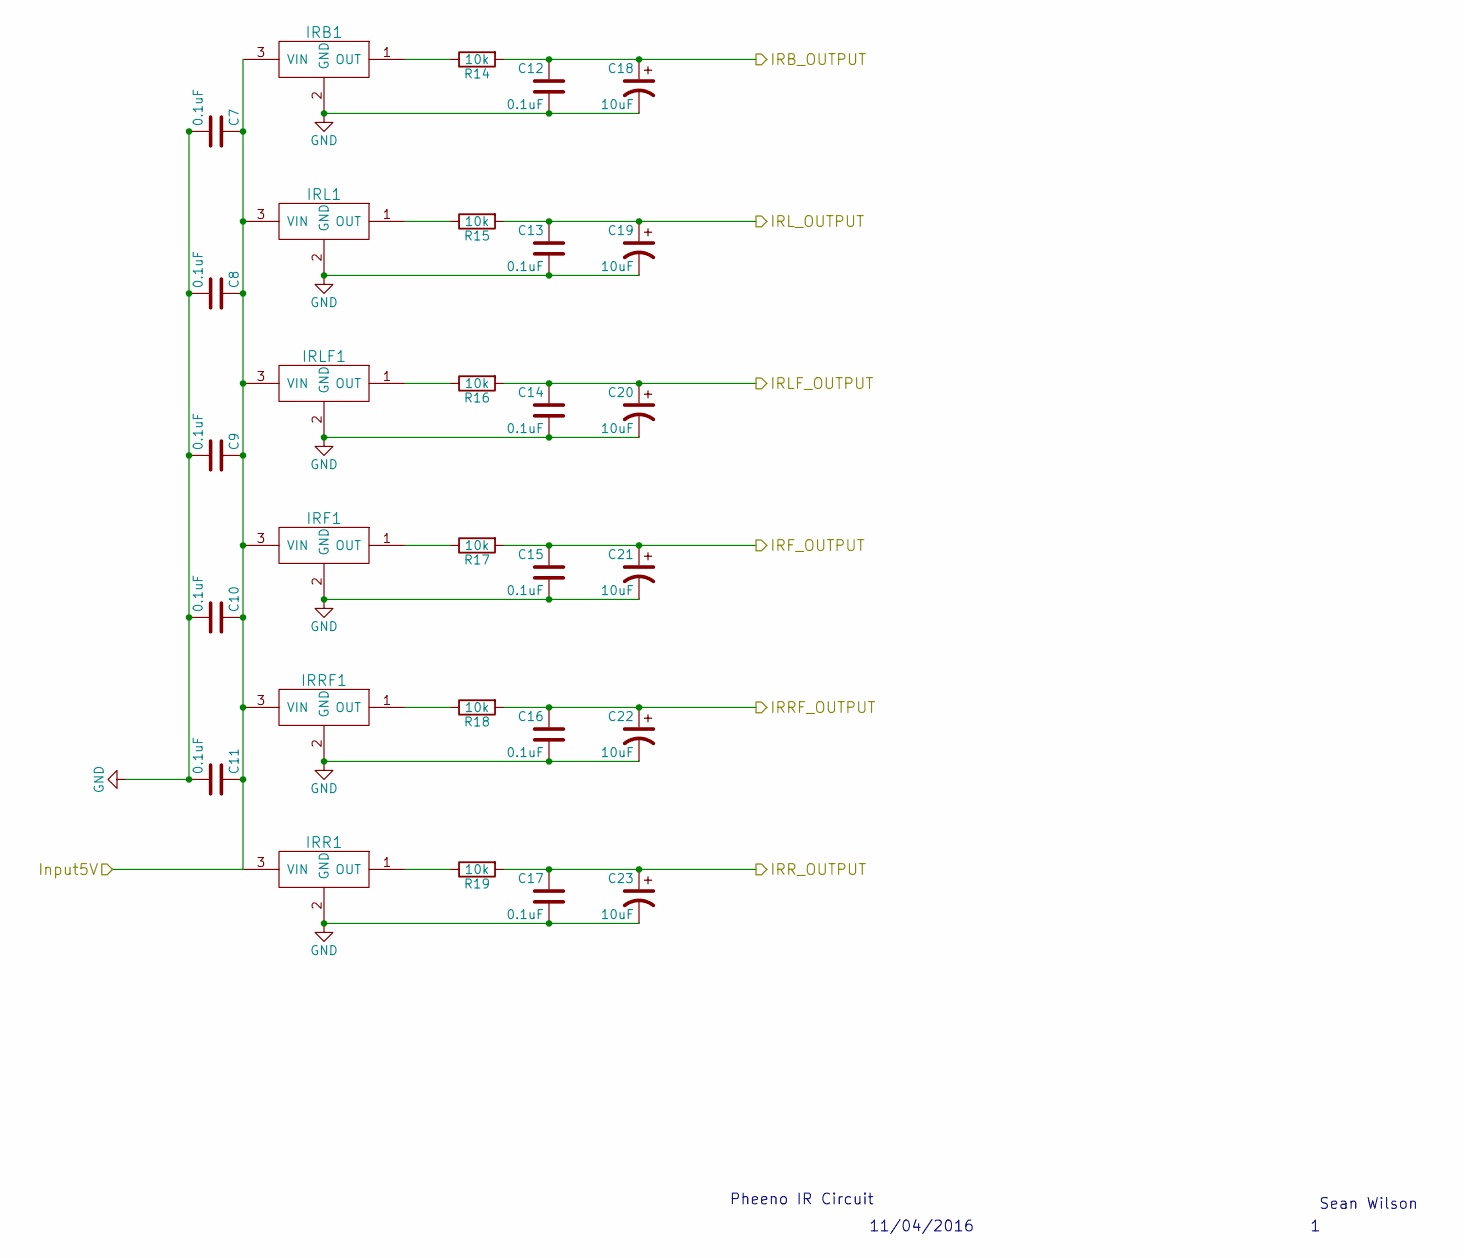
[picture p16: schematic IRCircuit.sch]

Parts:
C7, C8, C9, C10, C11, C12, C13, C14, C15, C16, C17: 0.1uF; C_Rect_L7_W2_P5
C18, C19, C20, C21, C22, C23: 10uF; C_Radial_D4_P1.5
IRB1: GP2Y0A41SK0F
IRF1: GP2Y0A41SK0F
IRL1: GP2Y0A41SK0F
IRLF1: GP2Y0A41SK0F
IRR1: GP2Y0A41SK0F
IRRF1: GP2Y0A41SK0F
R14, R15, R16, R17, R18, R19: 10k; Resistor_Horizontal_RM7mm

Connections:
/PheenoArduinoCircuit/IRB_Input: C12.1, C18.1, R14.2; also elsewhere on the board
/PheenoArduinoCircuit/IRF_Input: C15.1, C21.1, R17.2; also elsewhere on the board
/PheenoArduinoCircuit/IRLF_Input: C14.1, C20.1, R16.2; also elsewhere on the board
/PheenoArduinoCircuit/IRL_Input: C13.1, C19.1, R15.2; also elsewhere on the board
/PheenoArduinoCircuit/IRRF_Input: C16.1, C22.1, R18.2; also elsewhere on the board
/PheenoArduinoCircuit/IRR_Input: C17.1, C23.1, R19.2; also elsewhere on the board
/PheenoLowVoltageCutoff/IMUCircuit5V: C7.1, C8.1, C9.1, C10.1, C11.1, IRB1.3 (VIN), IRF1.3 (VIN), IRL1.3 (VIN), IRLF1.3 (VIN), IRR1.3 (VIN), IRRF1.3 (VIN); also elsewhere on the board
GND: C7.2, C8.2, C9.2, C10.2, C11.2, C12.2, C13.2, C14.2, C15.2, C16.2, C17.2, C18.2, C19.2, C20.2, C21.2, C22.2, C23.2, IRB1.2 (GND), IRF1.2 (GND), IRL1.2 (GND), IRLF1.2 (GND), IRR1.2 (GND), IRRF1.2 (GND); also elsewhere on the board
unnamed: IRB1.1 (OUT), R14.1
unnamed: IRF1.1 (OUT), R17.1
unnamed: IRL1.1 (OUT), R15.1
unnamed: IRLF1.1 (OUT), R16.1
unnamed: IRR1.1 (OUT), R19.1
unnamed: IRRF1.1 (OUT), R18.1

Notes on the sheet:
Pheeno IR Circuit
11/04/2016
Sean Wilson

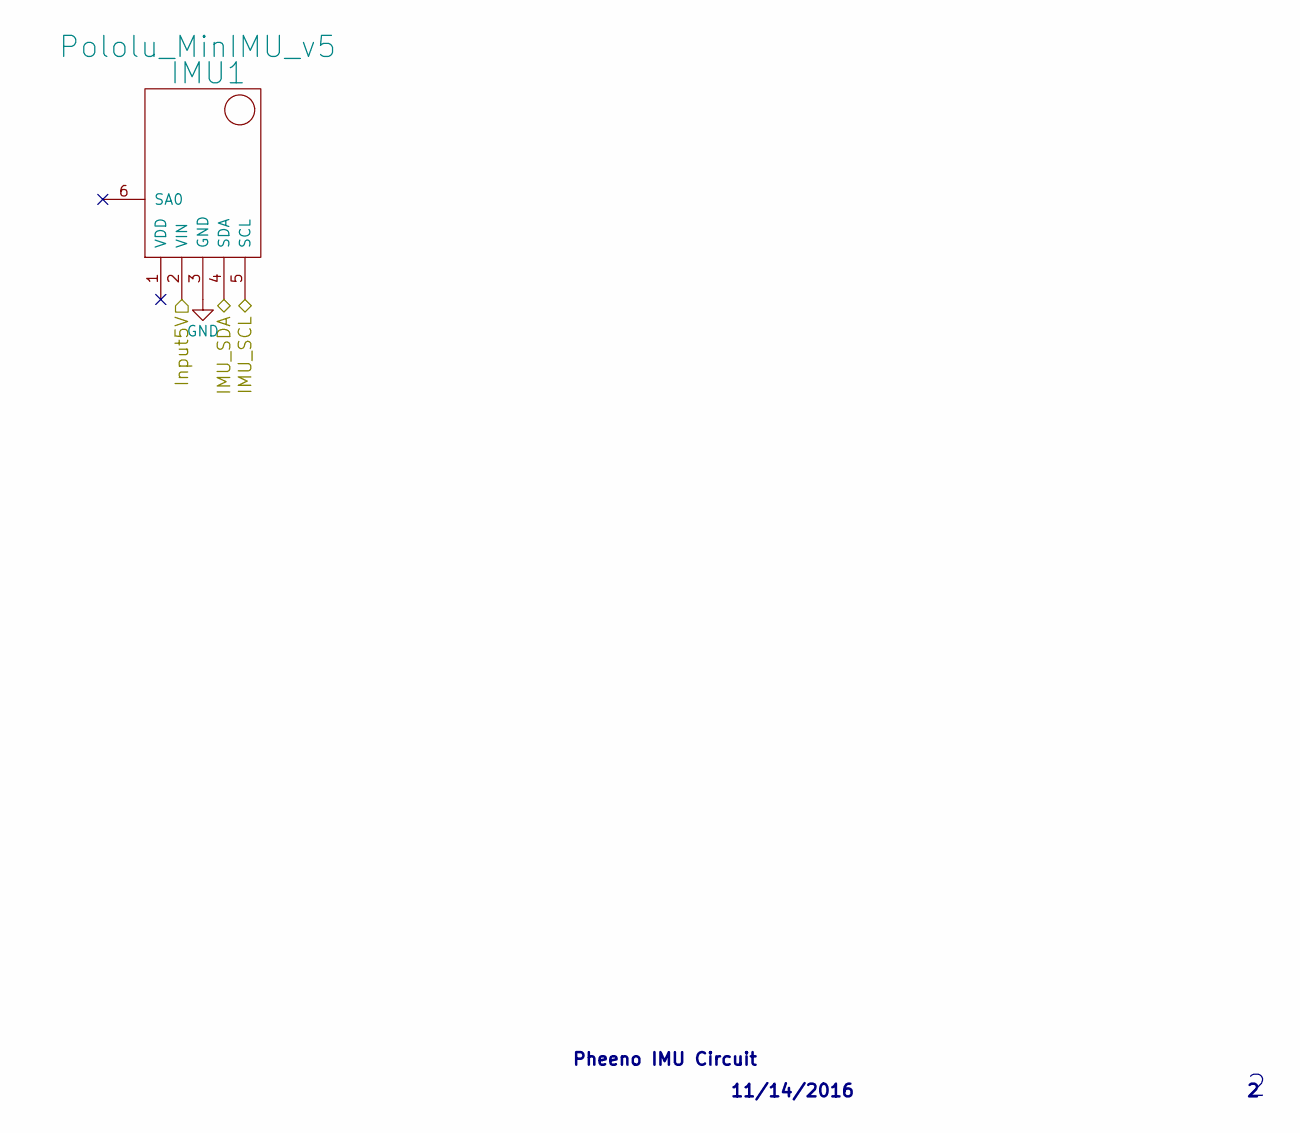
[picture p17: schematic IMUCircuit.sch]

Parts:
IMU1: Pololu_MinIMU_v5; Pololu_MiniIMU_v5

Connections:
/Pheeno IMU/IMU_SCL: IMU1.5 (SCL); also elsewhere on the board
/Pheeno IMU/IMU_SDA: IMU1.4 (SDA); also elsewhere on the board
/PheenoLowVoltageCutoff/IMUCircuit5V: IMU1.2 (VIN); also elsewhere on the board
GND: IMU1.3 (GND); also elsewhere on the board

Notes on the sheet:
Pheeno IMU Circuit
11/14/2016

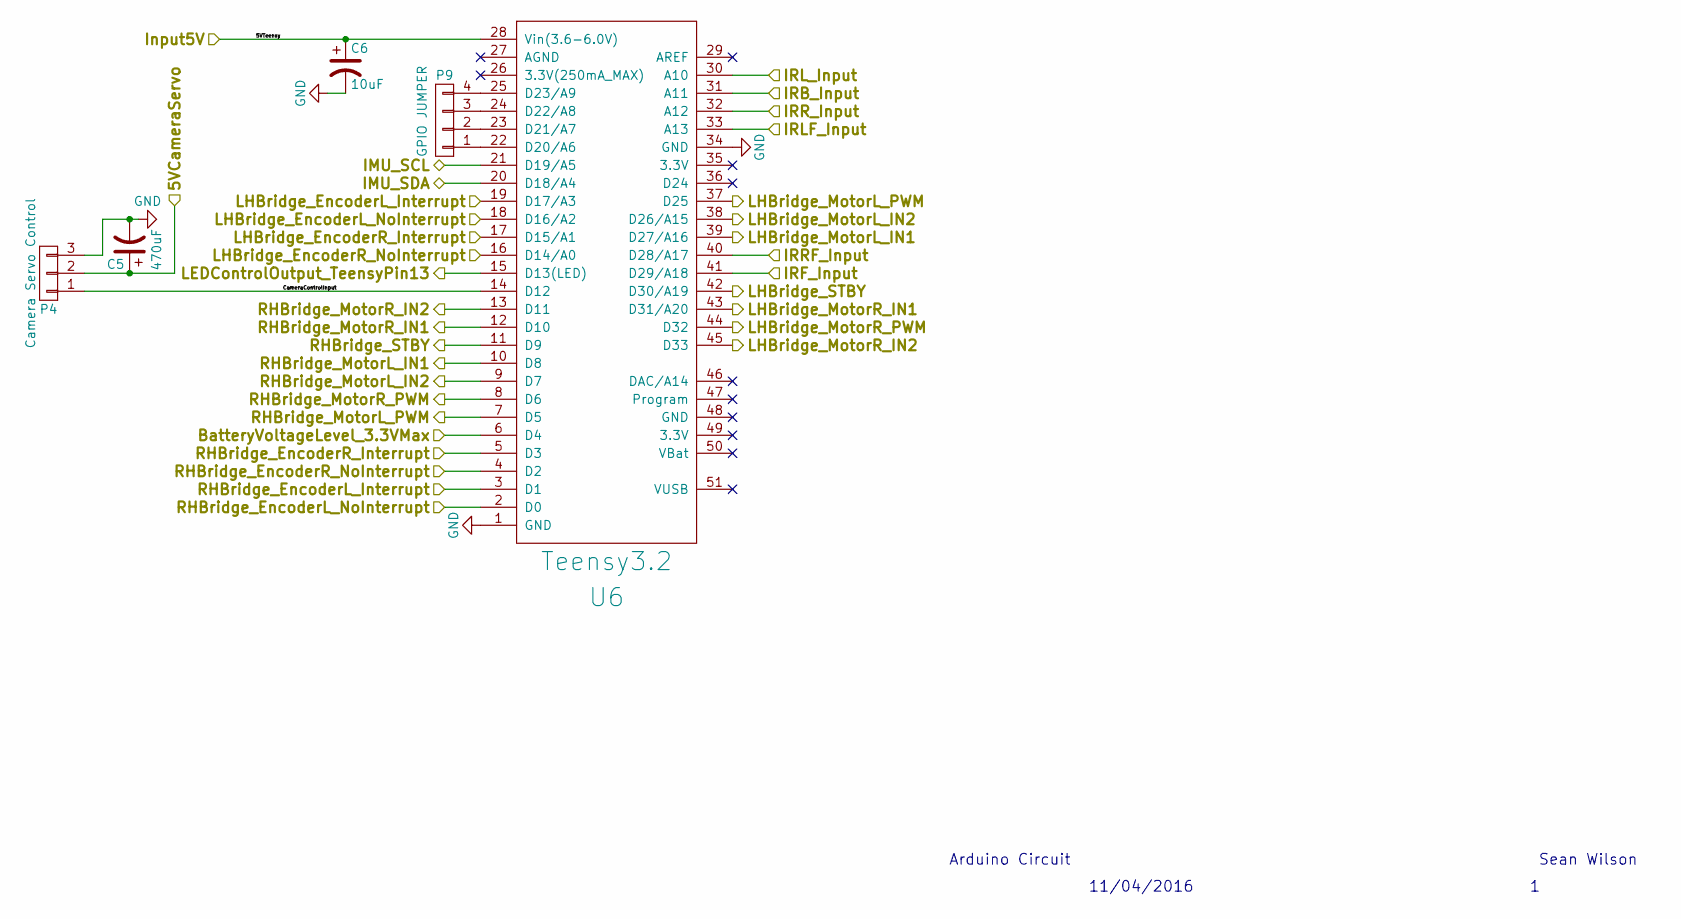
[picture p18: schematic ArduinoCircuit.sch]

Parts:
C5: 470uF; C_Radial_D10_L16_P5
C6: 10uF; C_Radial_D4_P1.5
P4: Camera Servo Control; Pin_Header_Straight_1x03
P9: GPIO JUMPER; Pin_Header_Straight_1x04
U6: Teensy3.2

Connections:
/Pheeno IMU/IMU_SCL: U6.21 (D19/A5); also elsewhere on the board
/Pheeno IMU/IMU_SDA: U6.20 (D18/A4); also elsewhere on the board
/PheenoArduinoCircuit/5VCameraServo: C5.1, P4.2; also elsewhere on the board
/PheenoArduinoCircuit/CameraControlInput: P4.1, U6.14 (D12)
/PheenoArduinoCircuit/IRB_Input: U6.31 (A11); also elsewhere on the board
/PheenoArduinoCircuit/IRF_Input: U6.41 (D29/A18); also elsewhere on the board
/PheenoArduinoCircuit/IRLF_Input: U6.33 (A13); also elsewhere on the board
/PheenoArduinoCircuit/IRL_Input: U6.30 (A10); also elsewhere on the board
/PheenoArduinoCircuit/IRRF_Input: U6.40 (D28/A17); also elsewhere on the board
/PheenoArduinoCircuit/IRR_Input: U6.32 (A12); also elsewhere on the board
/PheenoArduinoCircuit/LHBridge_EncoderL_Interrupt: U6.19 (D17/A3); also elsewhere on the board
/PheenoArduinoCircuit/LHBridge_EncoderL_NoInterrupt: U6.18 (D16/A2); also elsewhere on the board
/PheenoArduinoCircuit/LHBridge_EncoderR_Interrupt: U6.17 (D15/A1); also elsewhere on the board
/PheenoArduinoCircuit/LHBridge_EncoderR_NoInterrupt: U6.16 (D14/A0); also elsewhere on the board
/PheenoArduinoCircuit/LHBridge_MotorL_IN1: U6.39 (D27/A16); also elsewhere on the board
/PheenoArduinoCircuit/LHBridge_MotorL_IN2: U6.38 (D26/A15); also elsewhere on the board
/PheenoArduinoCircuit/LHBridge_MotorL_PWM: U6.37 (D25); also elsewhere on the board
/PheenoArduinoCircuit/LHBridge_MotorR_IN1: U6.43 (D31/A20); also elsewhere on the board
/PheenoArduinoCircuit/LHBridge_MotorR_IN2: U6.45 (D33); also elsewhere on the board
/PheenoArduinoCircuit/LHBridge_MotorR_PWM: U6.44 (D32); also elsewhere on the board
/PheenoArduinoCircuit/LHBridge_STBY: U6.42 (D30/A19); also elsewhere on the board
/PheenoArduinoCircuit/RHBridge_EncoderL_Interrupt: U6.3 (D1); also elsewhere on the board
/PheenoArduinoCircuit/RHBridge_EncoderL_NoInterrupt: U6.2 (D0); also elsewhere on the board
/PheenoArduinoCircuit/RHBridge_EncoderR_Interrupt: U6.5 (D3); also elsewhere on the board
/PheenoArduinoCircuit/RHBridge_EncoderR_NoInterrupt: U6.4 (D2); also elsewhere on the board
/PheenoArduinoCircuit/RHBridge_MotorL_IN1: U6.10 (D8); also elsewhere on the board
/PheenoArduinoCircuit/RHBridge_MotorL_IN2: U6.9 (D7); also elsewhere on the board
/PheenoArduinoCircuit/RHBridge_MotorL_PWM: U6.7 (D5); also elsewhere on the board
/PheenoArduinoCircuit/RHBridge_MotorR_IN1: U6.12 (D10); also elsewhere on the board
/PheenoArduinoCircuit/RHBridge_MotorR_IN2: U6.13 (D11); also elsewhere on the board
/PheenoArduinoCircuit/RHBridge_MotorR_PWM: U6.8 (D6); also elsewhere on the board
/PheenoArduinoCircuit/RHBridge_STBY: U6.11 (D9); also elsewhere on the board
/PheenoLEDCircuit/LEDControlInput_TeensyPin13: U6.15 (D13(LED)); also elsewhere on the board
/PheenoLowVoltageCutoff/BatteryVoltageLevel_3.3V: U6.6 (D4); also elsewhere on the board
/PheenoLowVoltageCutoff/IMUCircuit5V: C6.1, U6.28 (Vin(3.6-6.0V)); also elsewhere on the board
GND: C5.2, C6.2, P4.3, U6.1 (GND), U6.34 (GND); also elsewhere on the board
unnamed: P9.1, U6.22 (D20/A6)
unnamed: P9.2, U6.23 (D21/A7)
unnamed: P9.3, U6.24 (D22/A8)
unnamed: P9.4, U6.25 (D23/A9)

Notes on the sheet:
Arduino Circuit
Sean Wilson
11/04/2016

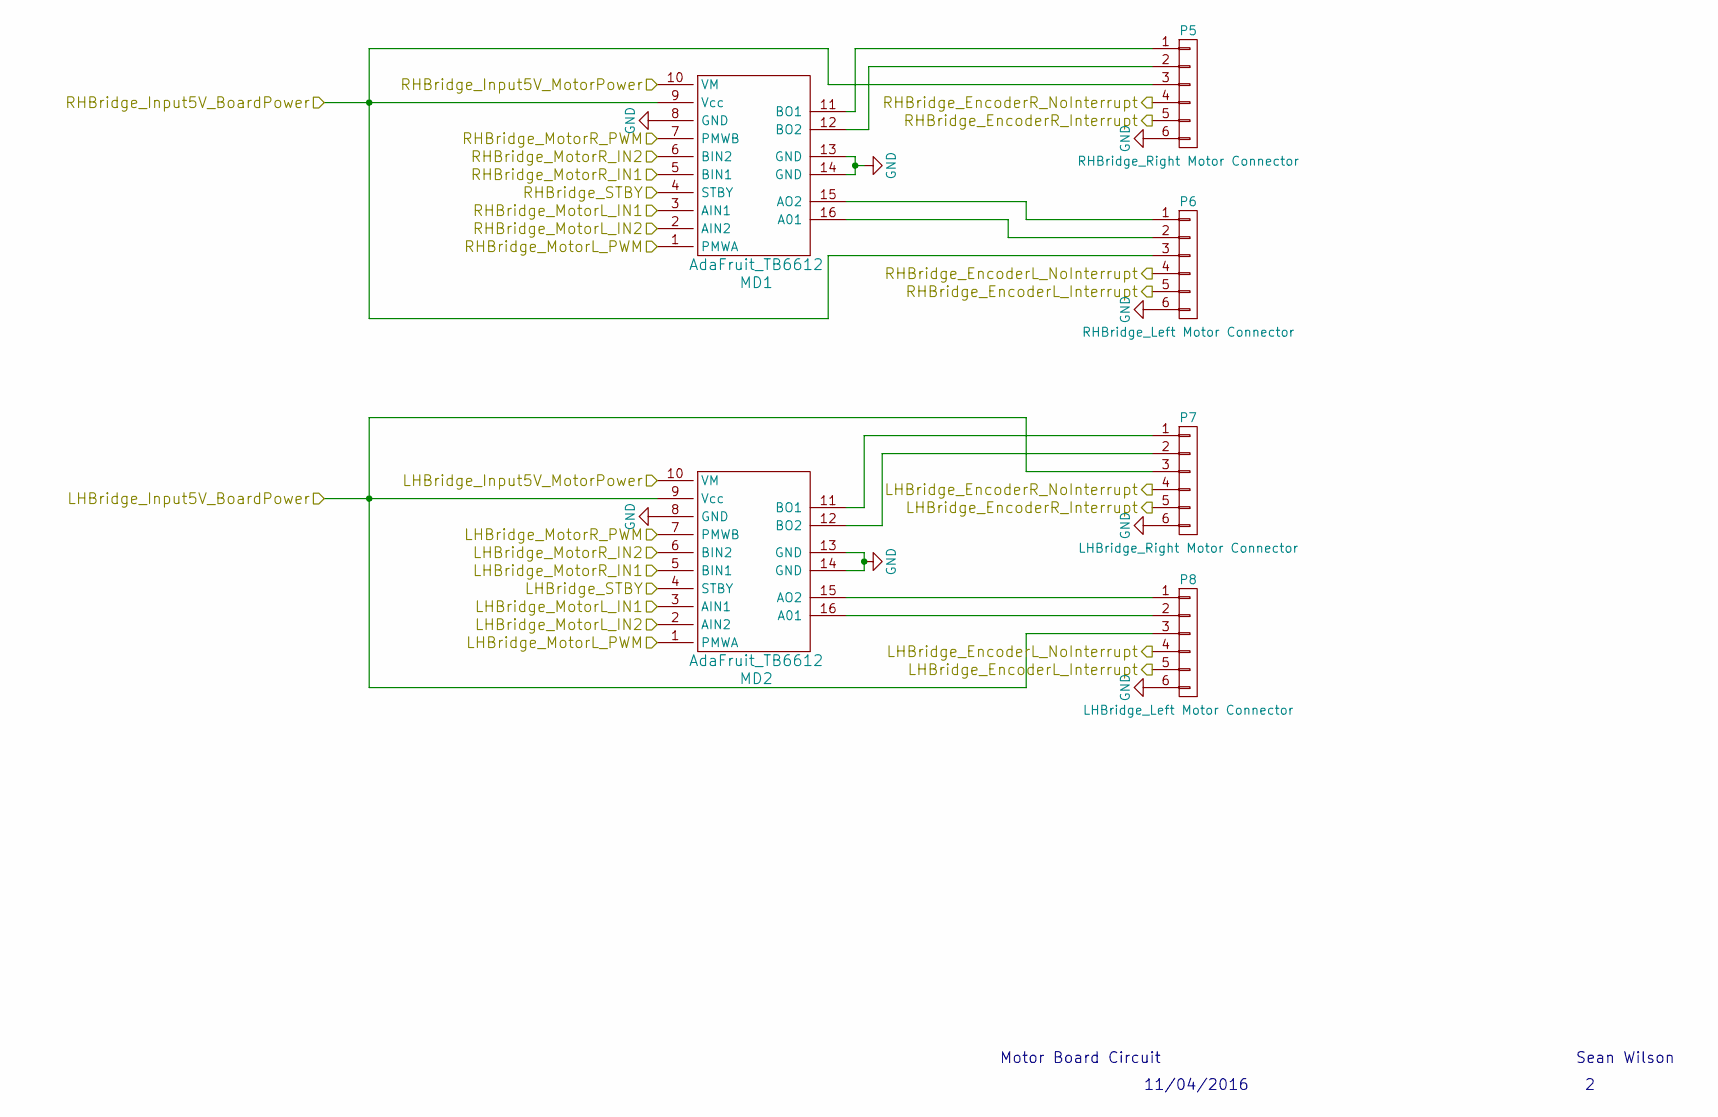
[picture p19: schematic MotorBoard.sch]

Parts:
MD1, MD2: AdaFruit_TB6612
P5: RHBridge_Right Motor Connector; Molex_KK-6410-06_06x2.54mm_Straight
P6: RHBridge_Left Motor Connector; Molex_KK-6410-06_06x2.54mm_Straight
P7: LHBridge_Right Motor Connector; Molex_KK-6410-06_06x2.54mm_Straight
P8: LHBridge_Left Motor Connector; Molex_KK-6410-06_06x2.54mm_Straight

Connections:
/PheenoArduinoCircuit/5VCameraServo: MD2.10 (VM); also elsewhere on the board
/PheenoArduinoCircuit/LHBridge_EncoderL_Interrupt: P8.5; also elsewhere on the board
/PheenoArduinoCircuit/LHBridge_EncoderL_NoInterrupt: P8.4; also elsewhere on the board
/PheenoArduinoCircuit/LHBridge_EncoderR_Interrupt: P7.5; also elsewhere on the board
/PheenoArduinoCircuit/LHBridge_EncoderR_NoInterrupt: P7.4; also elsewhere on the board
/PheenoArduinoCircuit/LHBridge_MotorL_IN1: MD2.3 (AIN1); also elsewhere on the board
/PheenoArduinoCircuit/LHBridge_MotorL_IN2: MD2.2 (AIN2); also elsewhere on the board
/PheenoArduinoCircuit/LHBridge_MotorL_PWM: MD2.1 (PMWA); also elsewhere on the board
/PheenoArduinoCircuit/LHBridge_MotorR_IN1: MD2.5 (BIN1); also elsewhere on the board
/PheenoArduinoCircuit/LHBridge_MotorR_IN2: MD2.6 (BIN2); also elsewhere on the board
/PheenoArduinoCircuit/LHBridge_MotorR_PWM: MD2.7 (PMWB); also elsewhere on the board
/PheenoArduinoCircuit/LHBridge_STBY: MD2.4 (STBY); also elsewhere on the board
/PheenoArduinoCircuit/RHBridge_EncoderL_Interrupt: P6.5; also elsewhere on the board
/PheenoArduinoCircuit/RHBridge_EncoderL_NoInterrupt: P6.4; also elsewhere on the board
/PheenoArduinoCircuit/RHBridge_EncoderR_Interrupt: P5.5; also elsewhere on the board
/PheenoArduinoCircuit/RHBridge_EncoderR_NoInterrupt: P5.4; also elsewhere on the board
/PheenoArduinoCircuit/RHBridge_MotorL_IN1: MD1.3 (AIN1); also elsewhere on the board
/PheenoArduinoCircuit/RHBridge_MotorL_IN2: MD1.2 (AIN2); also elsewhere on the board
/PheenoArduinoCircuit/RHBridge_MotorL_PWM: MD1.1 (PMWA); also elsewhere on the board
/PheenoArduinoCircuit/RHBridge_MotorR_IN1: MD1.5 (BIN1); also elsewhere on the board
/PheenoArduinoCircuit/RHBridge_MotorR_IN2: MD1.6 (BIN2); also elsewhere on the board
/PheenoArduinoCircuit/RHBridge_MotorR_PWM: MD1.7 (PMWB); also elsewhere on the board
/PheenoArduinoCircuit/RHBridge_STBY: MD1.4 (STBY); also elsewhere on the board
/PheenoLowVoltageCutoff/IMUCircuit5V: MD1.9 (Vcc), MD2.9 (Vcc), P5.3, P6.3, P7.3, P8.3; also elsewhere on the board
/PheenoMotorBoardCircuit/RHBridge_Input5V_MotorPower: MD1.10 (VM); also elsewhere on the board
GND: MD1.8 (GND), MD1.13 (GND), MD1.14 (GND), MD2.8 (GND), MD2.13 (GND), MD2.14 (GND), P5.6, P6.6, P7.6, P8.6; also elsewhere on the board
unnamed: MD1.11 (BO1), P5.1
unnamed: MD1.12 (BO2), P5.2
unnamed: MD1.15 (AO2), P6.1
unnamed: MD1.16 (A01), P6.2
unnamed: MD2.11 (BO1), P7.1
unnamed: MD2.12 (BO2), P7.2
unnamed: MD2.15 (AO2), P8.1
unnamed: MD2.16 (A01), P8.2

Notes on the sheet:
Motor Board Circuit
Sean Wilson
11/04/2016

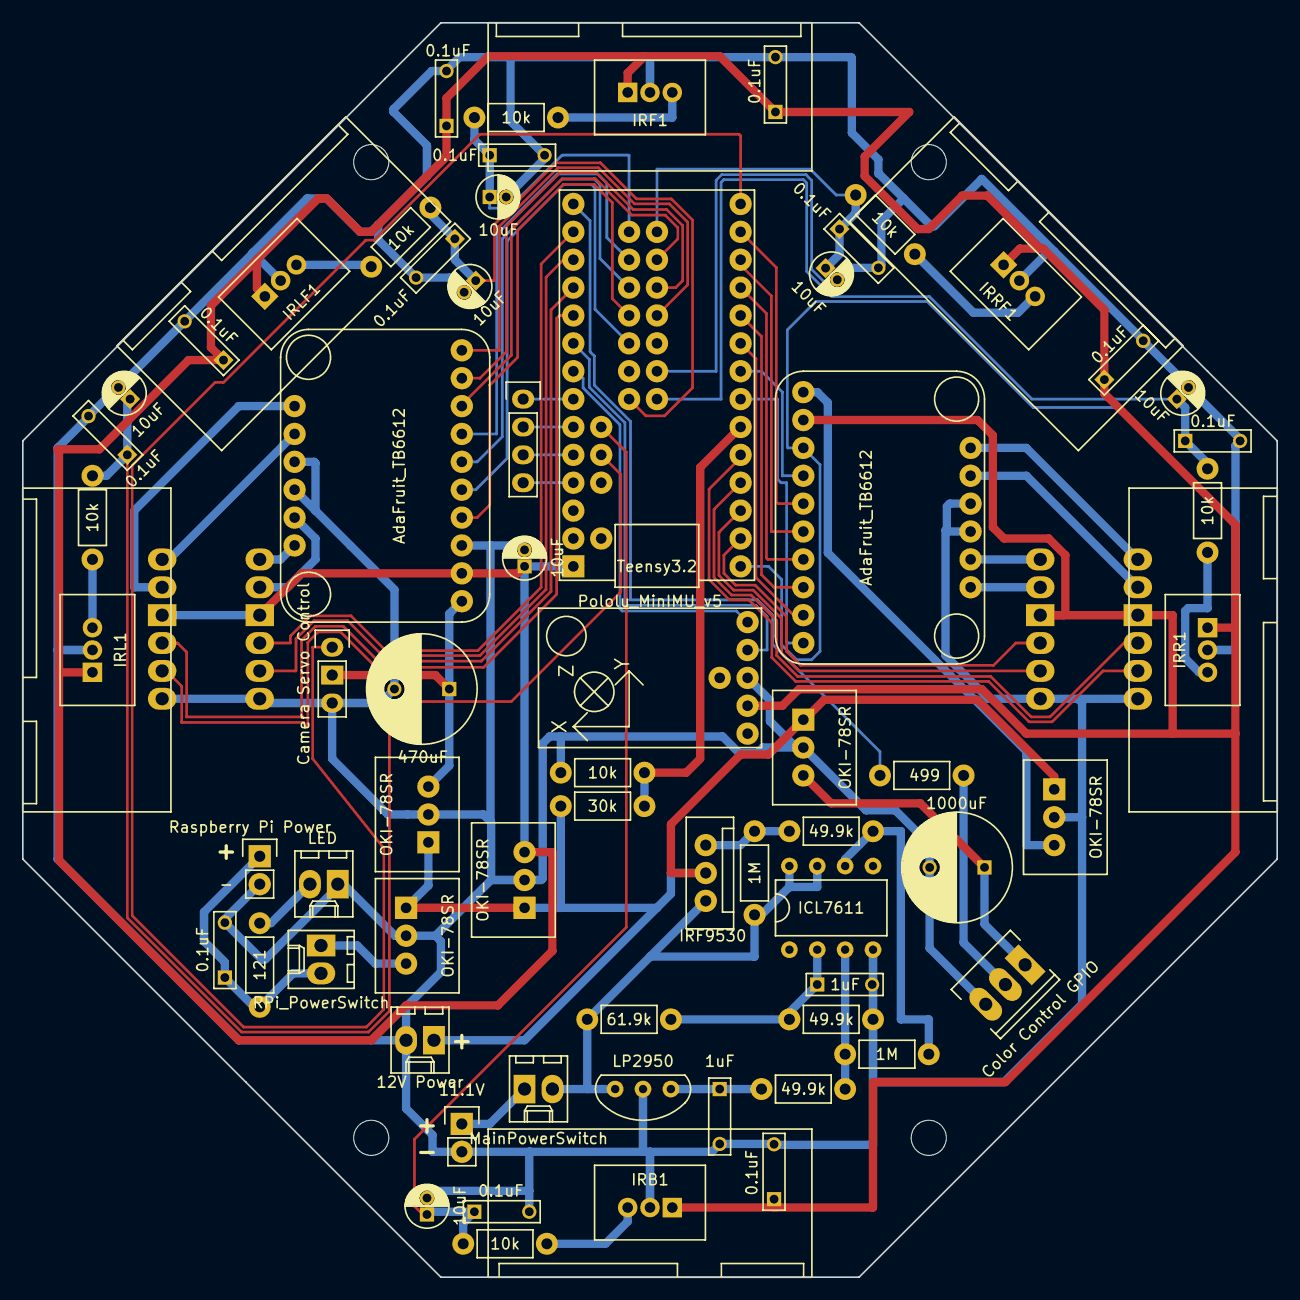
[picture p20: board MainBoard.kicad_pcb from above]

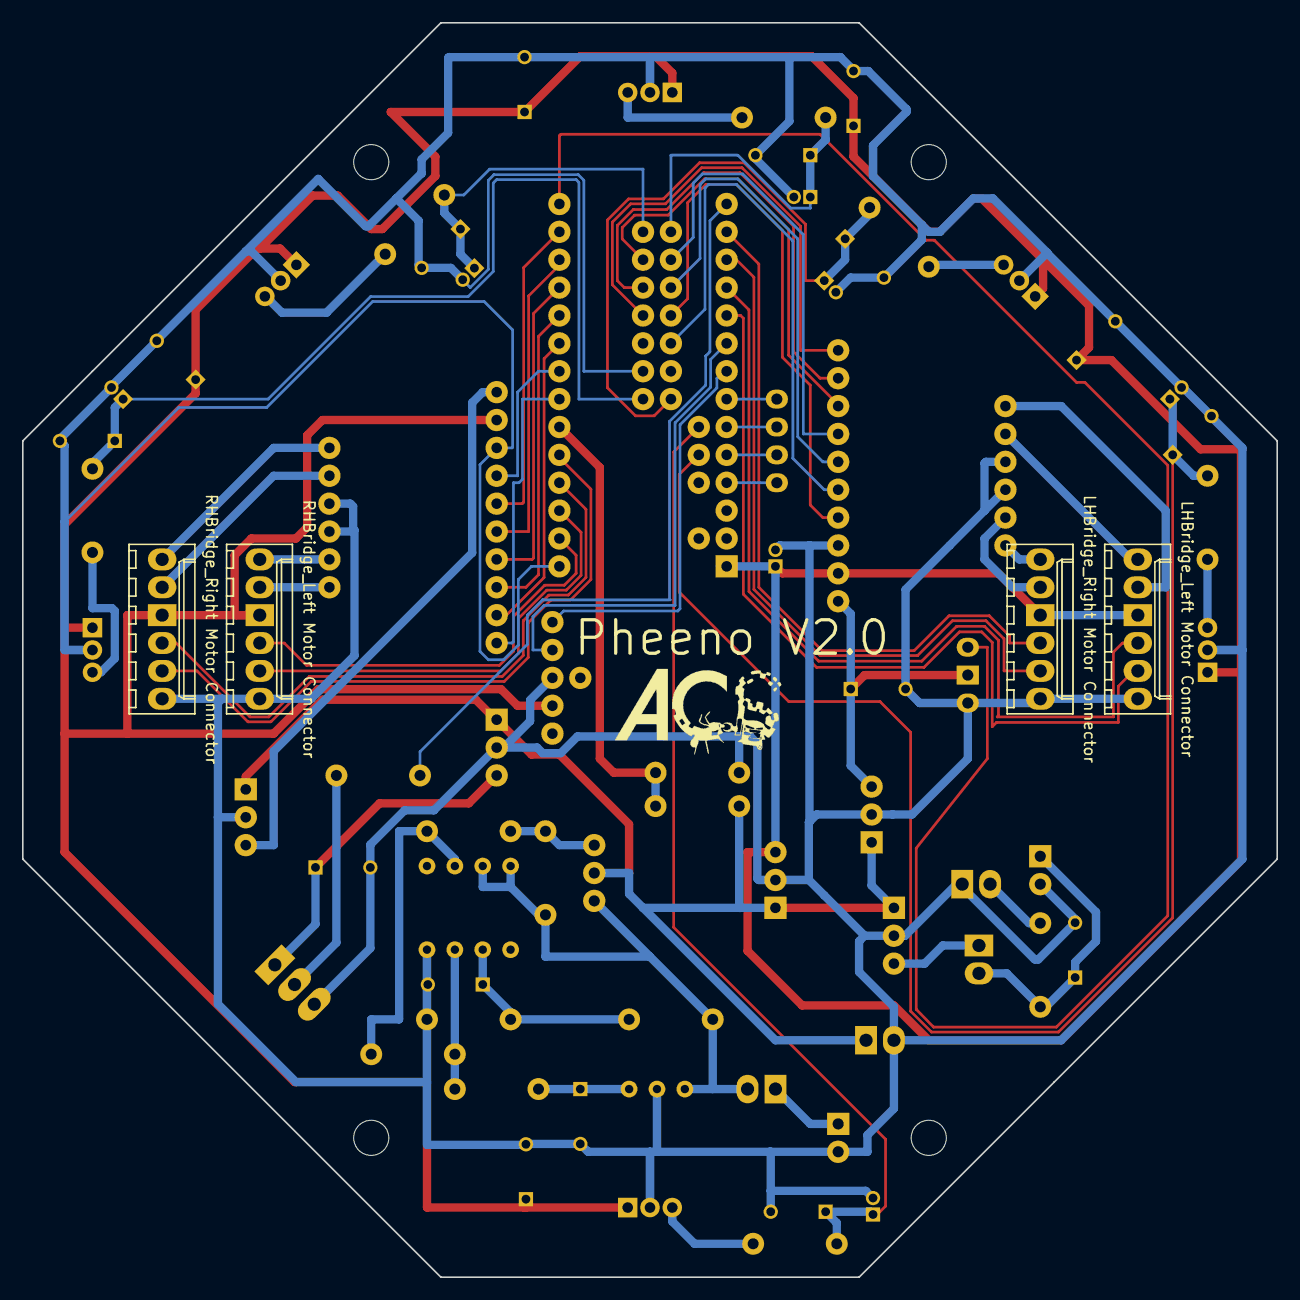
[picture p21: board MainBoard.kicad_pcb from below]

Board: 2 copper layers, 114.3 x 114.3 mm, 70 parts (4 on the bottom side), 68 nets.

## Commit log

2017-05-05 Initial Commit.
    [PheenoV1.dsn]
2018-01-20 Removed V1 files and added V2.
    [PheenoV1.dsn]
2018-01-20 Added v2 files.
    [ArduinoCircuit.sch, IMUCircuit.sch, IRCircuit.sch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]
